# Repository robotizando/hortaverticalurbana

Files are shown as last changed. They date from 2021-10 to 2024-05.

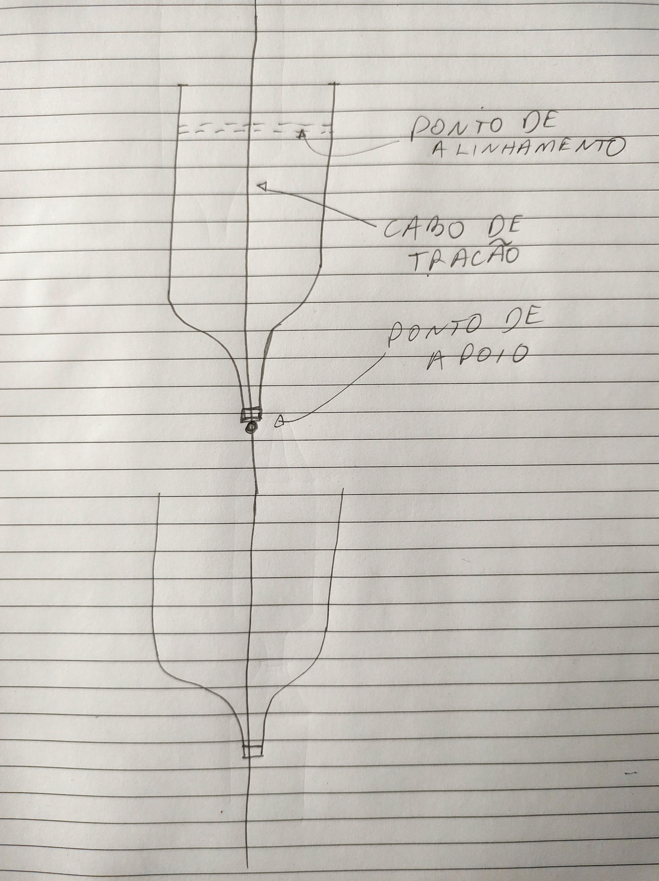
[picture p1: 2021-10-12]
Images/ponto de apoio invertido.jpg

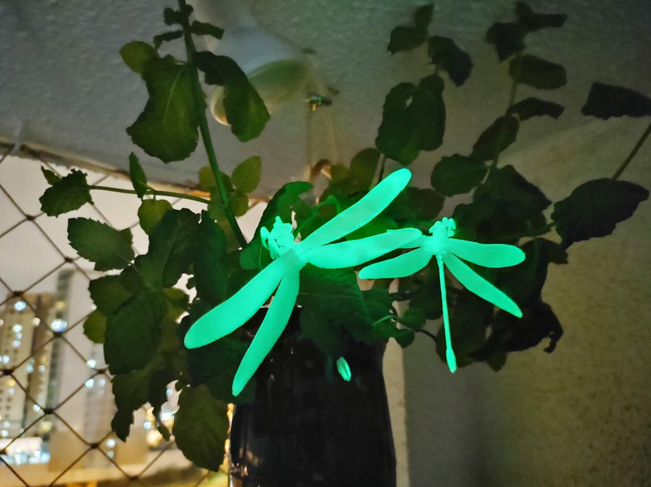
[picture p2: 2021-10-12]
Images/IMG_20210207_215612888_resized.jpg

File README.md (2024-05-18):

# Horta Vertical Urbana Livre

Repositório do material desenvolvido para a Horta Vertical Urbana

Veja o artigo completo **[no nosso site Robotizando](https://robotizando.com.br/pt-br/horta-vertical-urbana-livre/)**.

## Roadmap
- Terminar o sistema de agendamento de acionamento das cargas através de uma proto-linguagem

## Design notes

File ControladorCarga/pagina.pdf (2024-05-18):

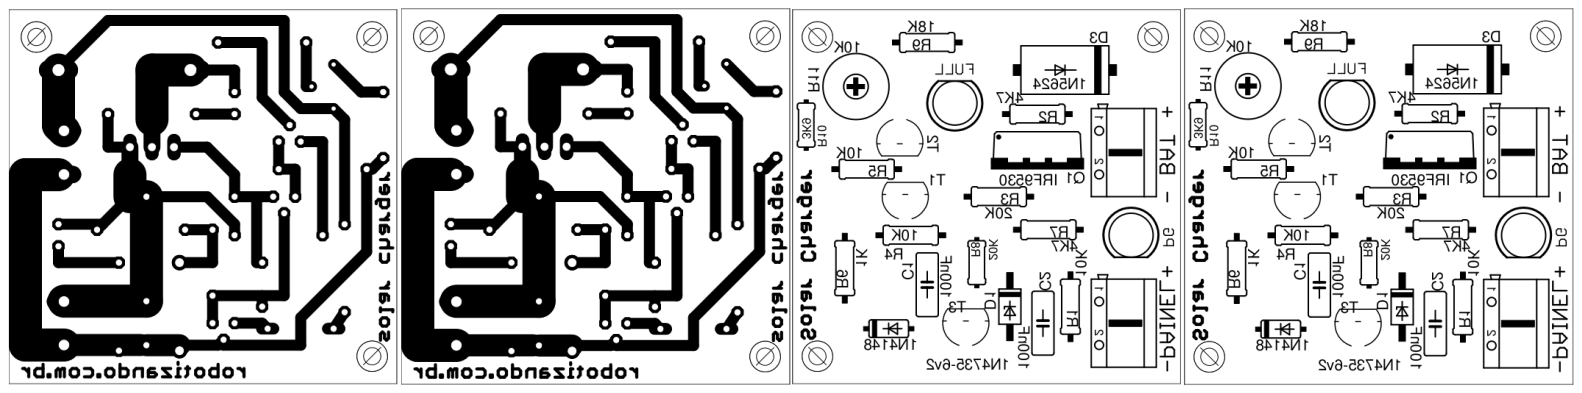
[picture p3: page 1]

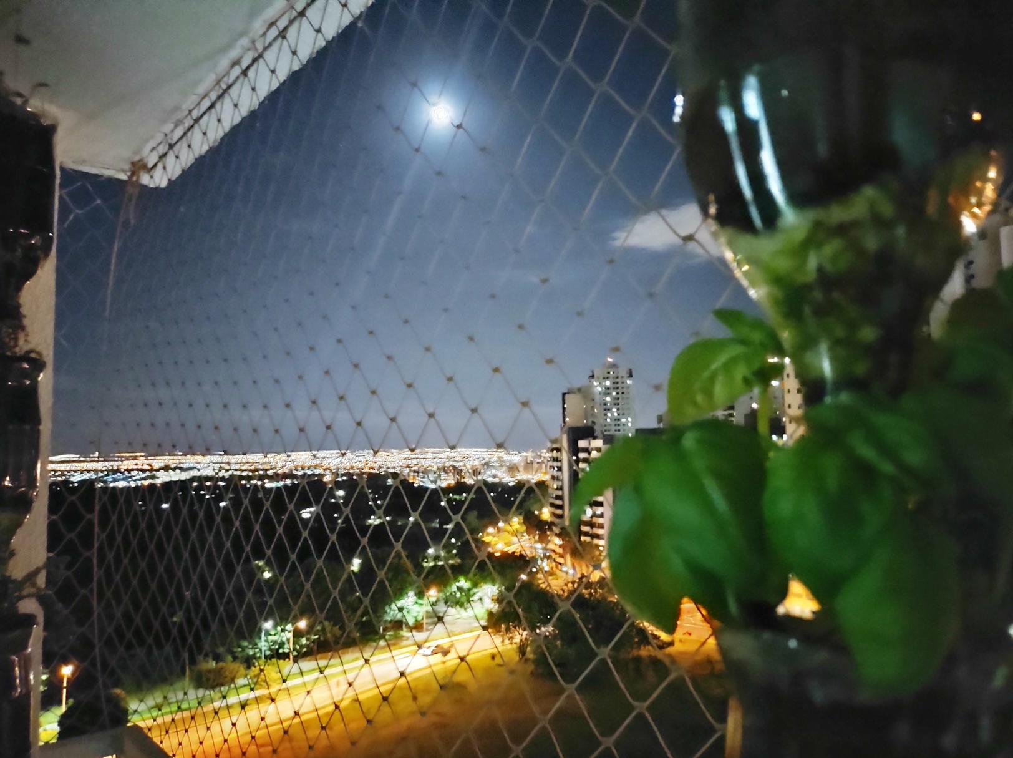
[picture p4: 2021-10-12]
Images/IMG_20210131_230912655_resized.jpg

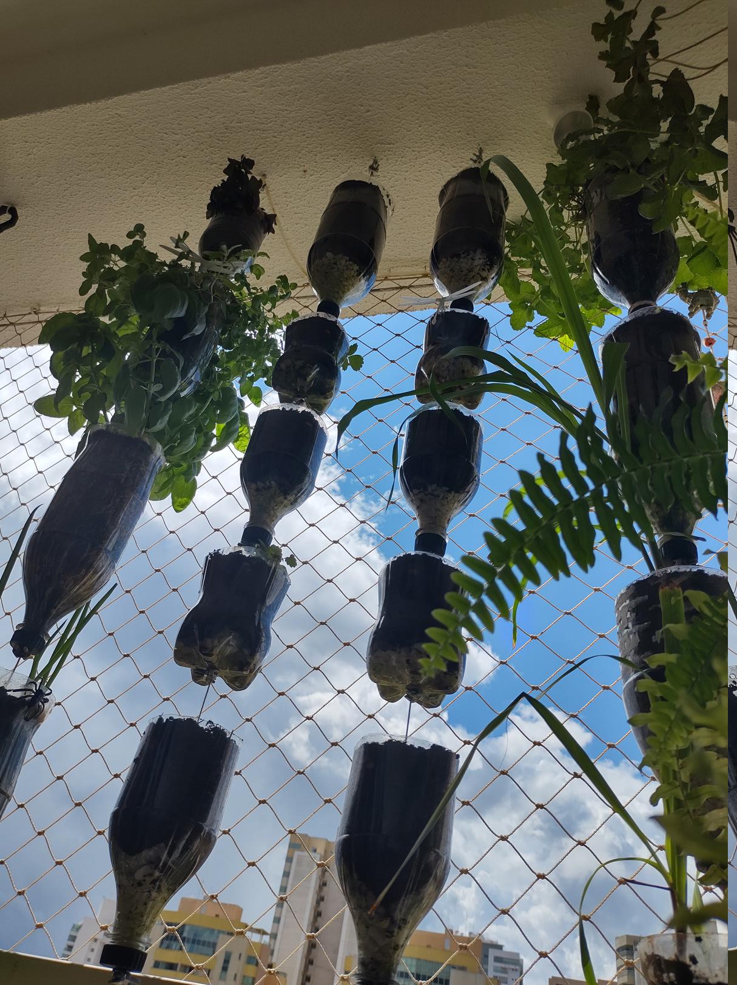
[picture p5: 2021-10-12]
Images/IMG_20210225_103853326_HDR_resized.jpg

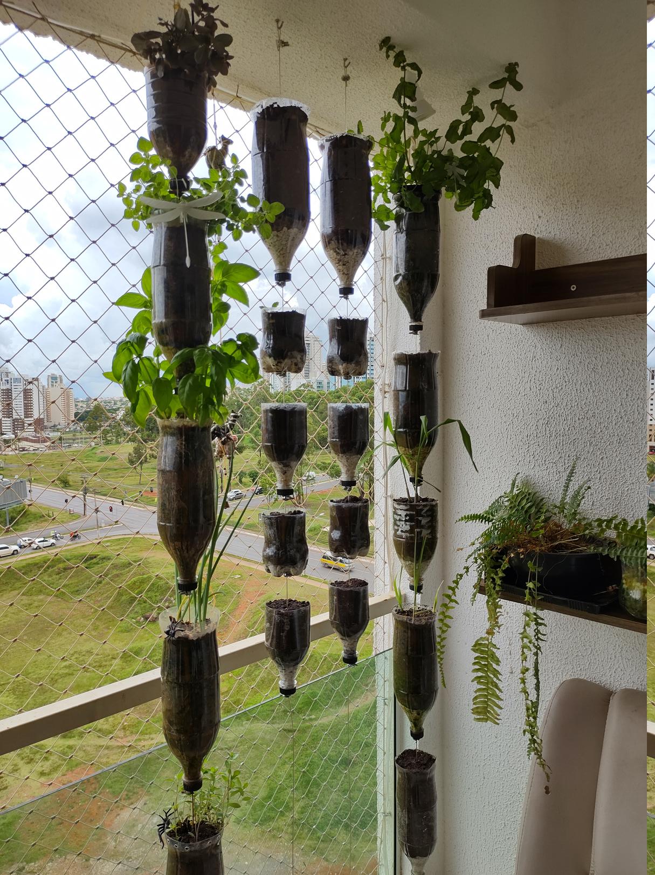
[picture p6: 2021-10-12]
Images/IMG_20210211_142128092_HDR_resized.jpg

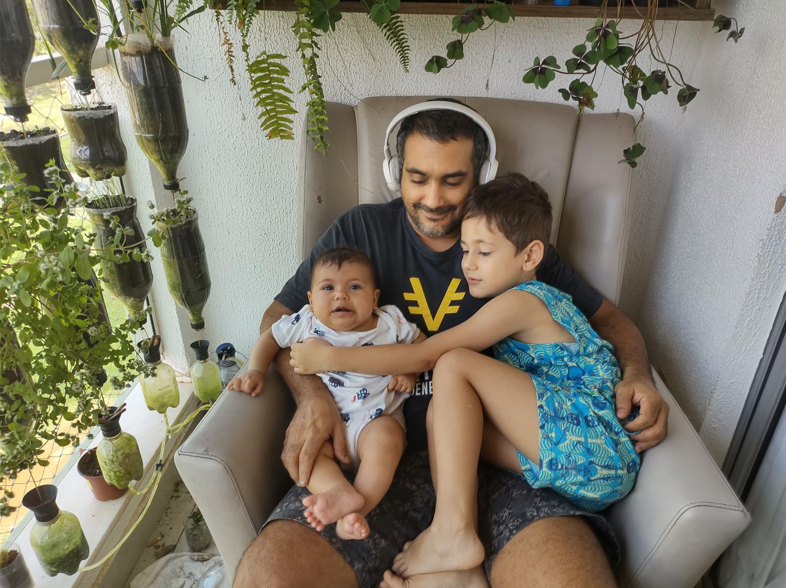
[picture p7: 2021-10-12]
Images/IMG_20210401_124431458_HDR_resized.jpg

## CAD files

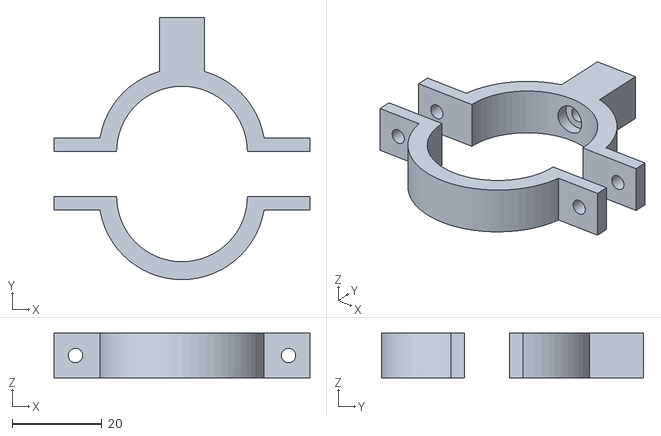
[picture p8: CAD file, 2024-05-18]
Pecas3D/caixa_holder.stl
57.2 x 58.6 x 10.0

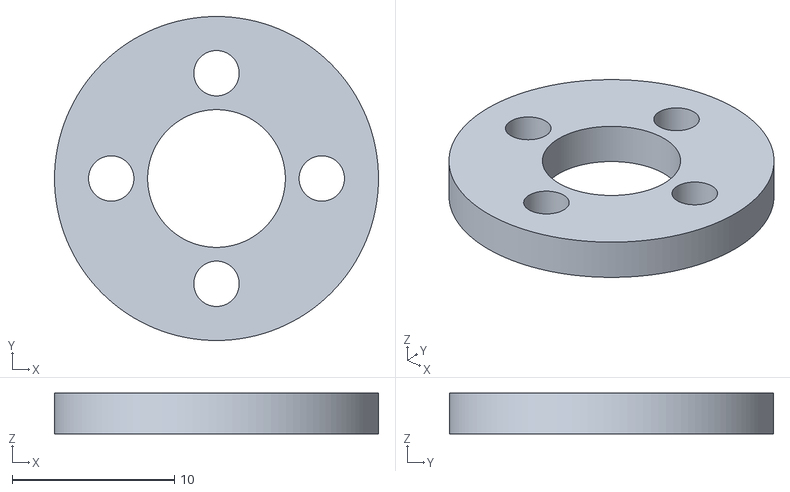
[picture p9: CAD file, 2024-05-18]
Pecas3D/respiro_pet_anel.stl
20.0 x 20.0 x 2.50

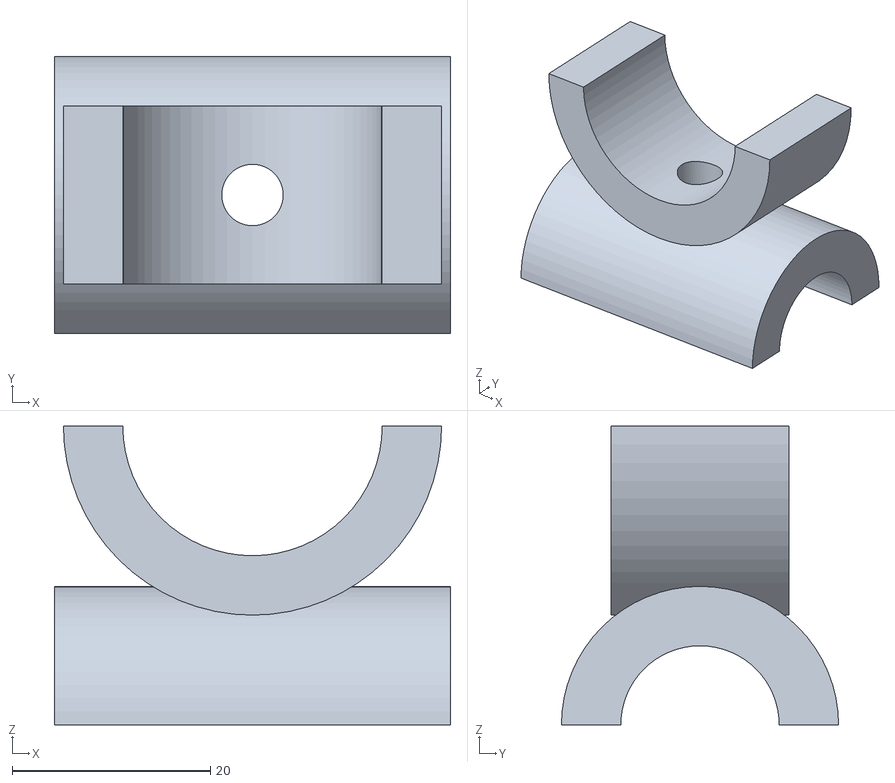
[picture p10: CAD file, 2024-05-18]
Pecas3D/trava_barra.stl
40.0 x 28.0 x 30.2

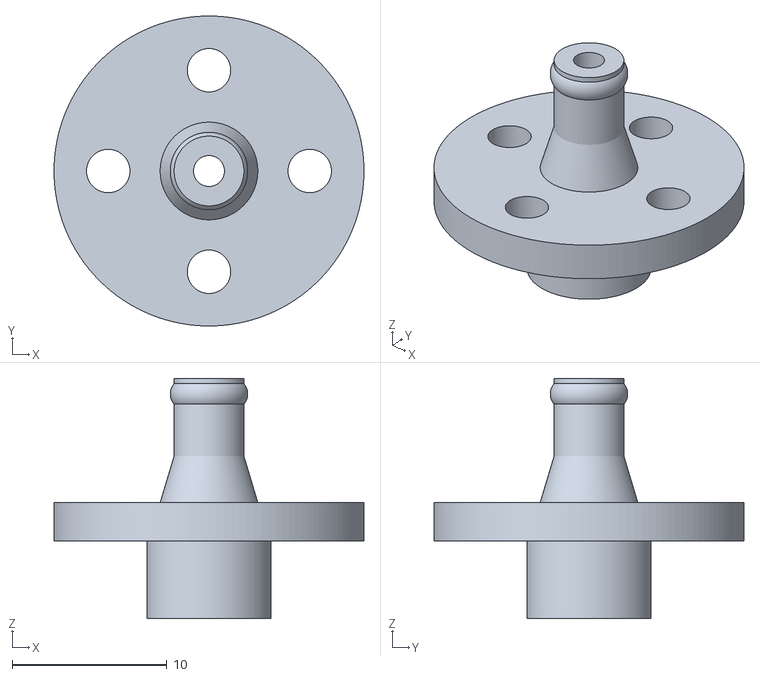
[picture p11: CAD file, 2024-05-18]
Pecas3D/respiro_pet_peca.stl
20.0 x 20.0 x 15.5

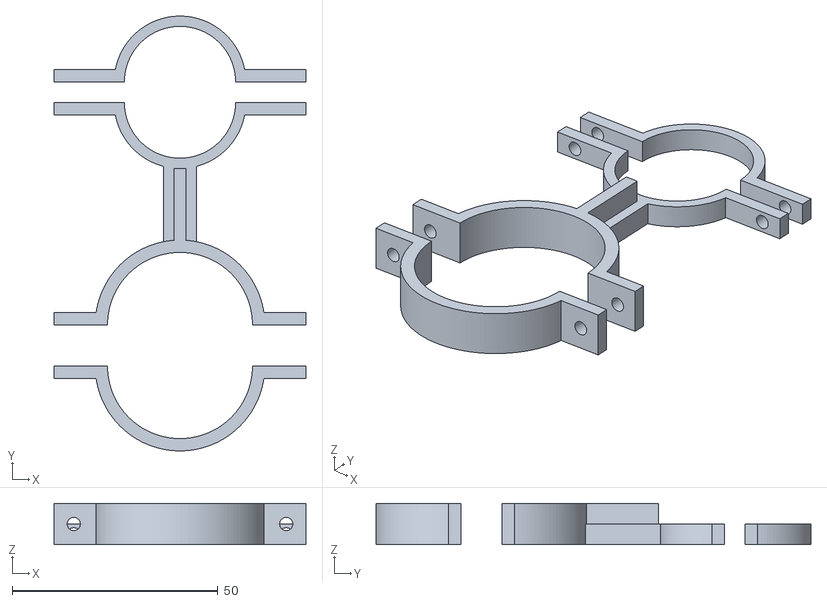
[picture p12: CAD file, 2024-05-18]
Pecas3D/buffer_superior_holder.stl
61.2 x 105.6 x 10.0

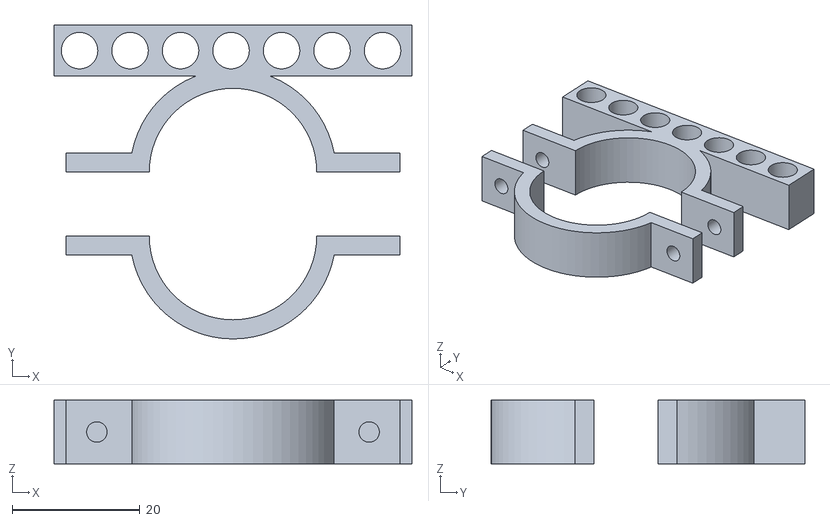
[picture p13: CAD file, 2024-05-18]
Pecas3D/canos_holder.stl
56.0 x 49.1 x 10.0

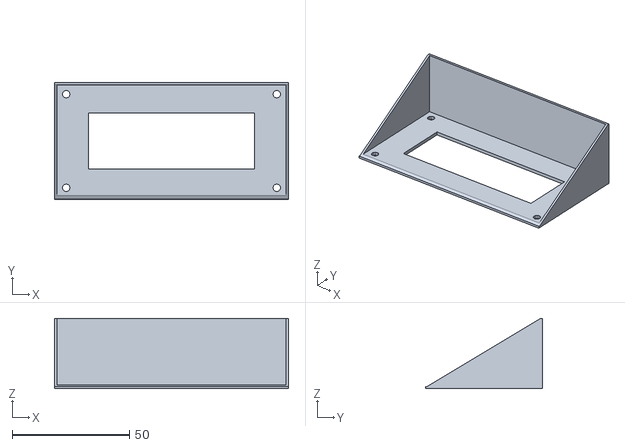
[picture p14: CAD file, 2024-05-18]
Pecas3D/ldc16x2sunshade.stl
100.0 x 50.0 x 30.0

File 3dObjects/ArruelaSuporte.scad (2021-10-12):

$fn=128;

hBase = 5;
dExterno = 45;
dInterno = 28.5;

dFuro = 6.5;


difference(){
    
    
    cylinder(h=hBase, r=dExterno/2);
    cylinder(h=hBase, r=dInterno/2);
    
    translate([-dInterno/2 - (dExterno-dInterno)/4 ,0,0])
    scale([0.6,1,1])
    cylinder(h=hBase, r=dFuro/2);

    translate([dInterno/2 + (dExterno-dInterno)/4 ,0,0])
    scale([0.6,1,1])
    cylinder(h=hBase, r=dFuro/2);

    translate([0 ,-dInterno/2 - (dExterno-dInterno)/4,0])
        scale([1,0.6,1])
    cylinder(h=hBase, r=dFuro/2);
    
    translate([0, dInterno/2 + (dExterno-dInterno)/4,0])
    scale([1,0.6,1])
    cylinder(h=hBase, r=dFuro/2);
    
}

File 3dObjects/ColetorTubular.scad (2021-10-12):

$fn=32;

dIntCone = 34;
dExtCone = dIntCone + 3;
hCone = 43;


hBico=8;
dIntBico=2.5;
dExtBico=5.1;

dIntAba = dExtCone;
dExtAba = dIntAba + 8;
hAba = 1;



*translate([0,0,hCone-0.1])
    tampa(bicos=1);




difference(){
    cylinder(h=hAba, r=dExtAba/2);
    cylinder(h=hAba, r=dIntAba/2);
}

difference(){
    cylinder(h=hCone, r=dExtCone/2);
    cylinder(h=hCone, r=dIntCone/2);

translate([dExtCone/2-3,25,3])
rotate([90,0,0])
cylinder(h=50,r=1);

translate([-dExtCone/2+3,25,3])
rotate([90,0,0])
cylinder(h=50,r=1);

}







module tampa(bicos=1){
  
    if(bicos==1){
        translate([0,0,dExtCone/2-1.7]){
            bico();
        }
    }
    
    if(bicos==2){
        translate([0,0,0]){
            translate([-5,0,dExtCone/2-3])
            bico();

            translate([5,0,dExtCone/2-3])
            bico();
        }
    }   
        
    difference(){

        sphere(r=dExtCone/2);
        sphere(r=dIntCone/2);
        
        if(bicos==2){
            translate([0,0,0]){
                translate([-5,0,dExtCone/2-5])
                bico(false);

                translate([5,0,dExtCone/2-5])
                bico(false);
            }
        }   
         
        if(bicos==1){
            translate([0,0,0]){
                translate([0,0,dExtCone/2-5])
                bico(false);
            }
        }
        
        translate([-dExtCone/2, -dExtCone/2,-dExtCone/2])
            cube([dExtCone,dExtCone,dExtCone/2]);    
    }
}




module bico(furado=true){
    difference(){
        
        render(){
            cylinder(h=hBico, r=dExtBico/2);
        
            translate([0,0, hBico-2])
            rotate_extrude(convexity = 10)
            translate([1.7, 0, 0])
            circle(r = 1, $fn = 100);
        }
        
        if(furado)
            cylinder(h=hBico, r=dIntBico/2);
    }
}

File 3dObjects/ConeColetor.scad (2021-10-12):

use <threadlib/threadlib.scad>



$fn = 256;

dBaseAro = 25;
dTopoAro = 45;
hCone = 25;
parede = 1.4;




*nut("PCO-1881", turns=3, Douter=34);



*difference(){
    import("3dponics-drip-nozzle-v2.stl");
    
    difference(){
        cylinder(h=10, r=30);
        cylinder(h=10, r=16.5);
    }    

    translate([0,0,9.95])
    color("red")
        cylinder(h=15.2, r=9);
}


//cone


translate([0,0,10]){

    //cone
    difference(){
        cylinder(h=hCone, r1=dBaseAro/2, r2=dTopoAro/2);
        cylinder(h=hCone, r1=(dBaseAro/2)-parede/2, r2=(dTopoAro/2)-parede/2);
    }


    //base
    dBase = 30;
    hBase = 1;
    dFuro = 2.5;
    difference(){
        cylinder(h=hBase, r=dBase/2);
        cylinder(h=hBase, r=dFuro/2);
        
        for ( i = [0 : 5] ){
            rotate( i * 60, [0, 0, 1])
            translate([-6.5,0,0])
            cylinder(h=hBase, r=dFuro/2);
        }
    }

    hPino = 5;
    dPino = 8;
    
    difference(){
        cylinder(h=hPino, r=dPino/2);
        cylinder(h=hPino, r=dFuro/2);
    }

    
    
}

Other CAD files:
3dObjects/ladrao01.scad
3dObjects/PontaGarrafa.scad
Pecas3D/buffer_superior_holder.scad
Pecas3D/caixa_holder.scad
Pecas3D/canos_holder.scad
Pecas3D/ldc16x2sunshade.scad
Pecas3D/respiro_pet.scad
Pecas3D/trava_barra.scad

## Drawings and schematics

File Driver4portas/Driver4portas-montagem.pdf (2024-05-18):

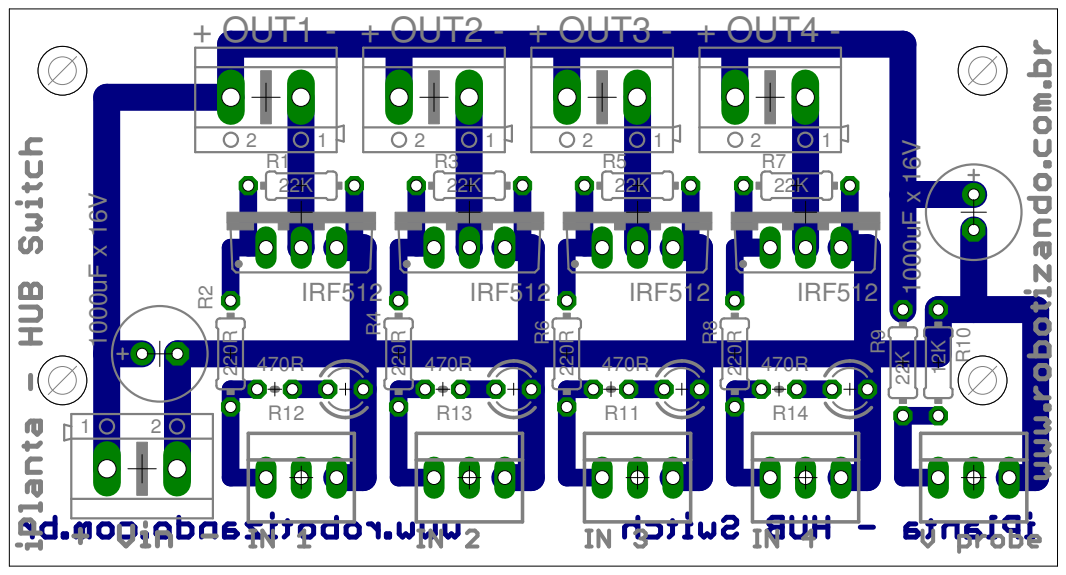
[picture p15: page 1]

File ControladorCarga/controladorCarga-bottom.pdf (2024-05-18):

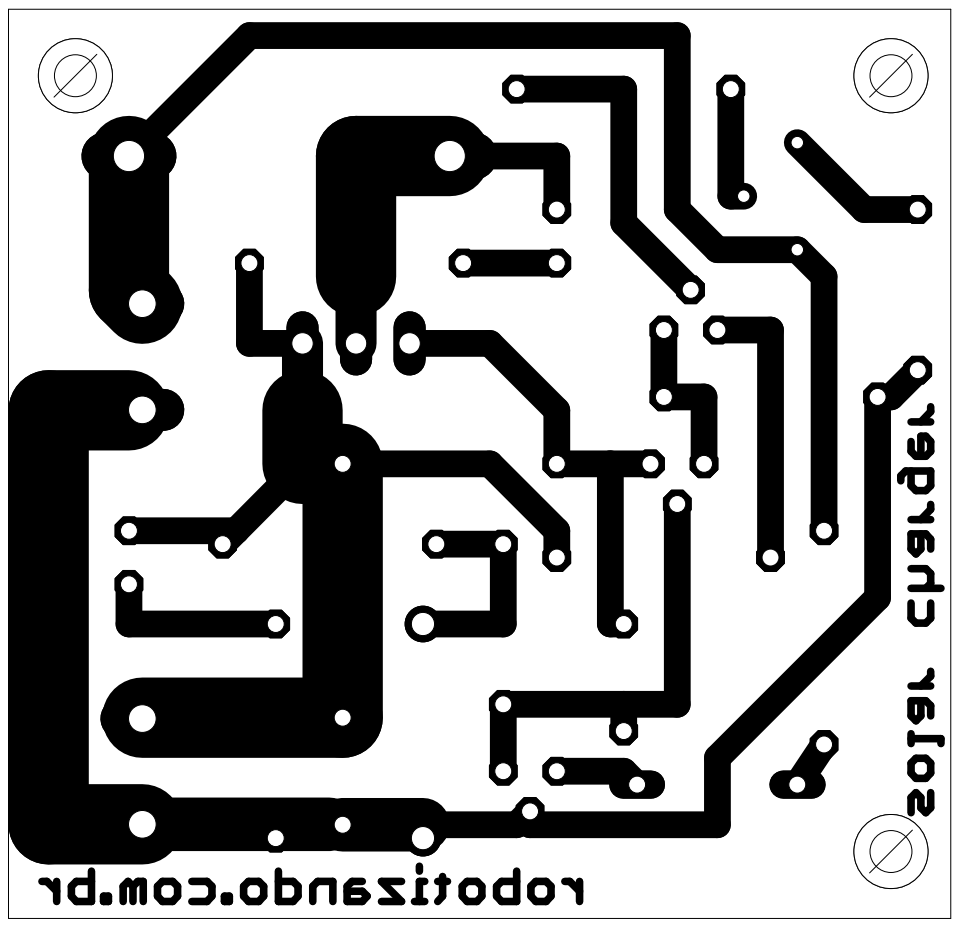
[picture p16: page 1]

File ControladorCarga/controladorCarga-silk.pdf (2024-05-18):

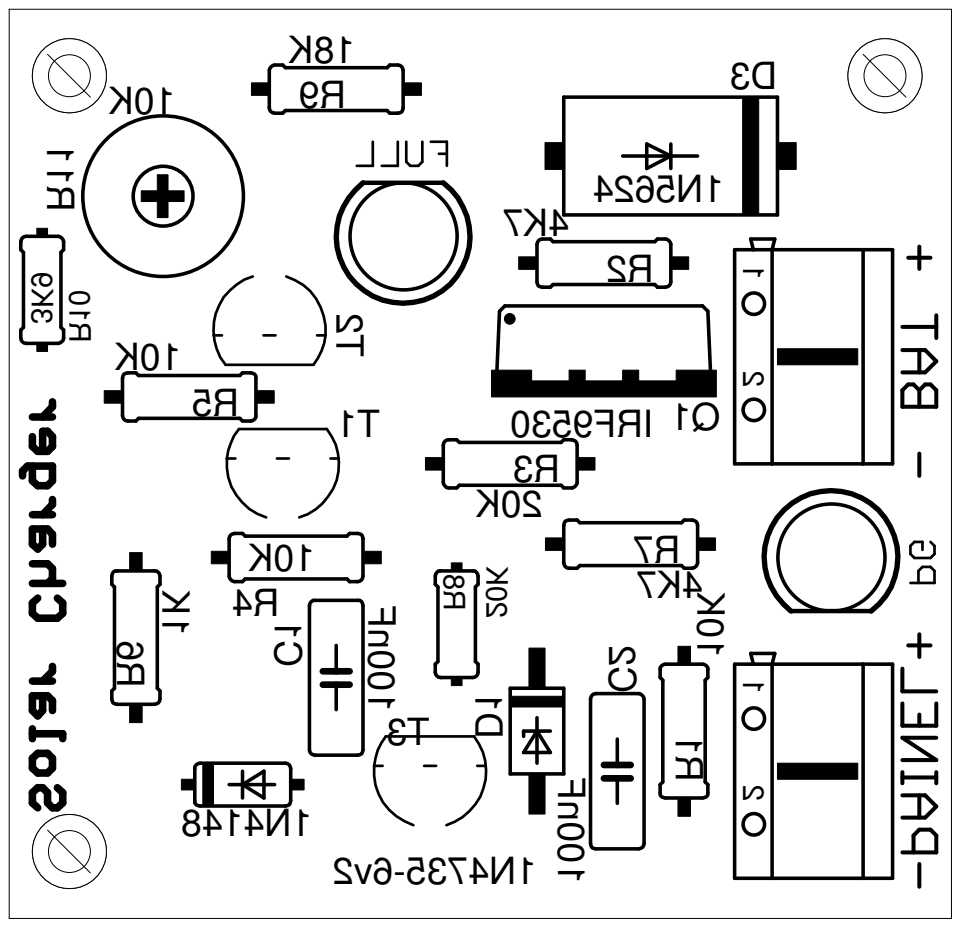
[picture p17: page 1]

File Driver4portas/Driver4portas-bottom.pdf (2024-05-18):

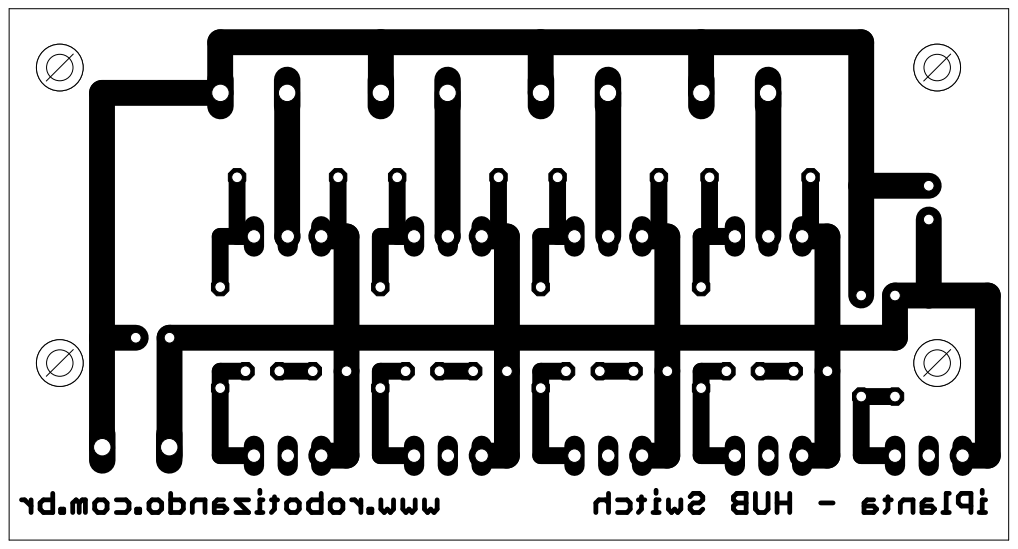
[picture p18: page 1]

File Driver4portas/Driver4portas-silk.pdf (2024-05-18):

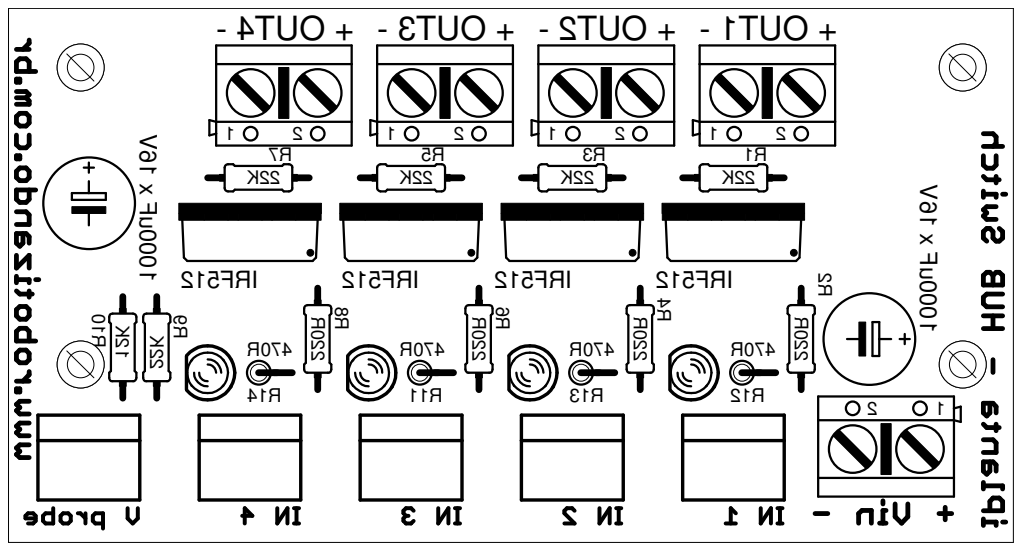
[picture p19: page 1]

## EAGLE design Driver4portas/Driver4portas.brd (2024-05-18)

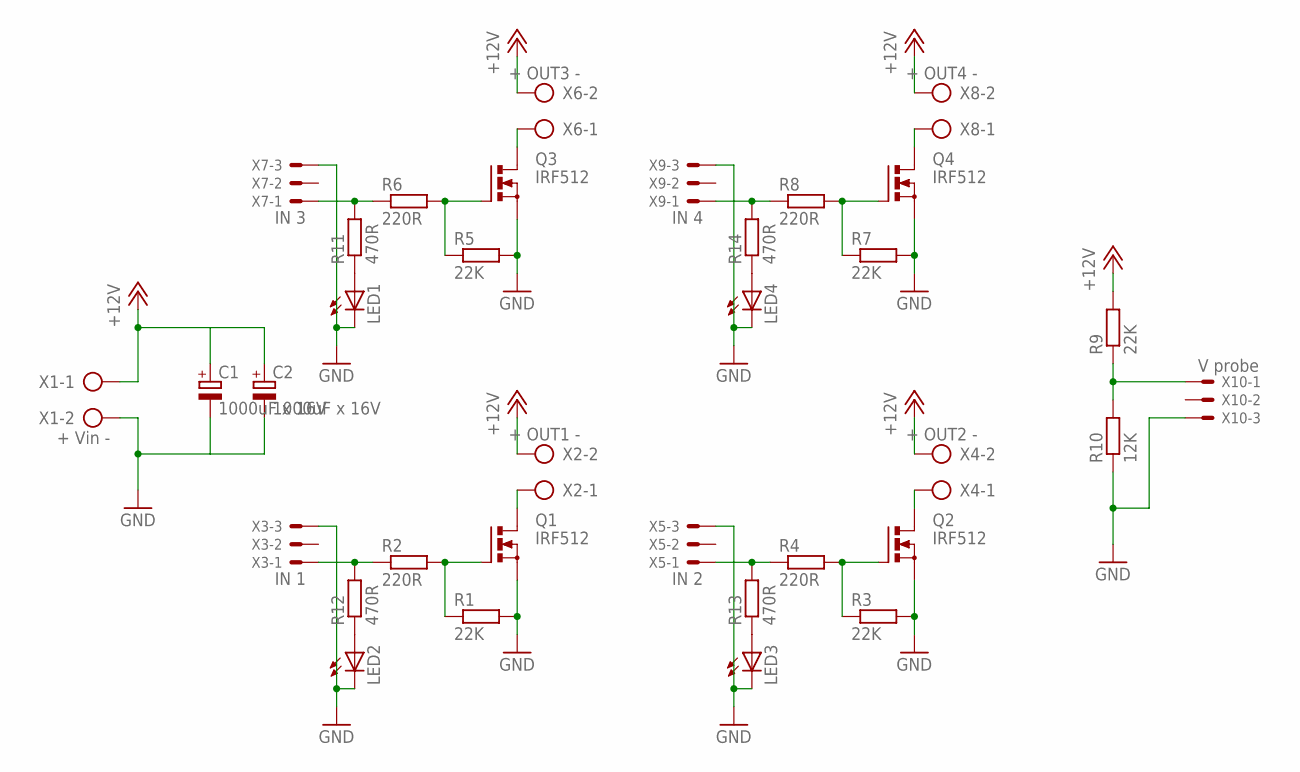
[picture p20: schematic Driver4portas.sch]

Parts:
C1, C2: 1000uF x 16V; E2,5-7
LED1, LED2, LED3, LED4: LED3MM
Q1, Q2, Q3, Q4: IRF512; TO220BV
R1, R3, R5, R7, R9: 22K; 0204/7
R2, R4, R6, R8: 220R; 0204/7
R10: 12K; 0204/7
R11, R12, R13, R14: 470R; 0204V
X1: + Vin -; AK500/2
X2: + OUT1 -; AK500/2
X3: IN 1; 22-23-2031
X4: + OUT2 -; AK500/2
X5: IN 2; 22-23-2031
X6: + OUT3 -; AK500/2
X7: IN 3; 22-23-2031
X8: + OUT4 -; AK500/2
X9: IN 4; 22-23-2031
X10: V probe; 22-23-2031

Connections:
+12V: C1.+, C2.+, R9.2, X1.1, X2.2, X4.2, X6.2, X8.2
GND: C1.-, C2.-, LED1.K (C), LED2.K (C), LED3.K (C), LED4.K (C), Q1.S, Q2.S, Q3.S, Q4.S, R1.2, R3.2, R5.2, R7.2, R10.1, X1.2, X3.3, X5.3, X7.3, X9.3, X10.3
unnamed: R2.1, R12.2, X3.1
unnamed: Q1.G, R1.1, R2.2
unnamed: Q1.D, X2.1
unnamed: Q2.G, R3.1, R4.2
unnamed: Q2.D, X4.1
unnamed: R4.1, R13.2, X5.1
unnamed: Q3.G, R5.1, R6.2
unnamed: Q3.D, X6.1
unnamed: R6.1, R11.2, X7.1
unnamed: Q4.G, R7.1, R8.2
unnamed: Q4.D, X8.1
unnamed: R8.1, R14.2, X9.1
unnamed: R9.1, R10.2, X10.1
unnamed: LED1.A, R11.1
unnamed: LED2.A, R12.1
unnamed: LED3.A, R13.1
unnamed: LED4.A, R14.1

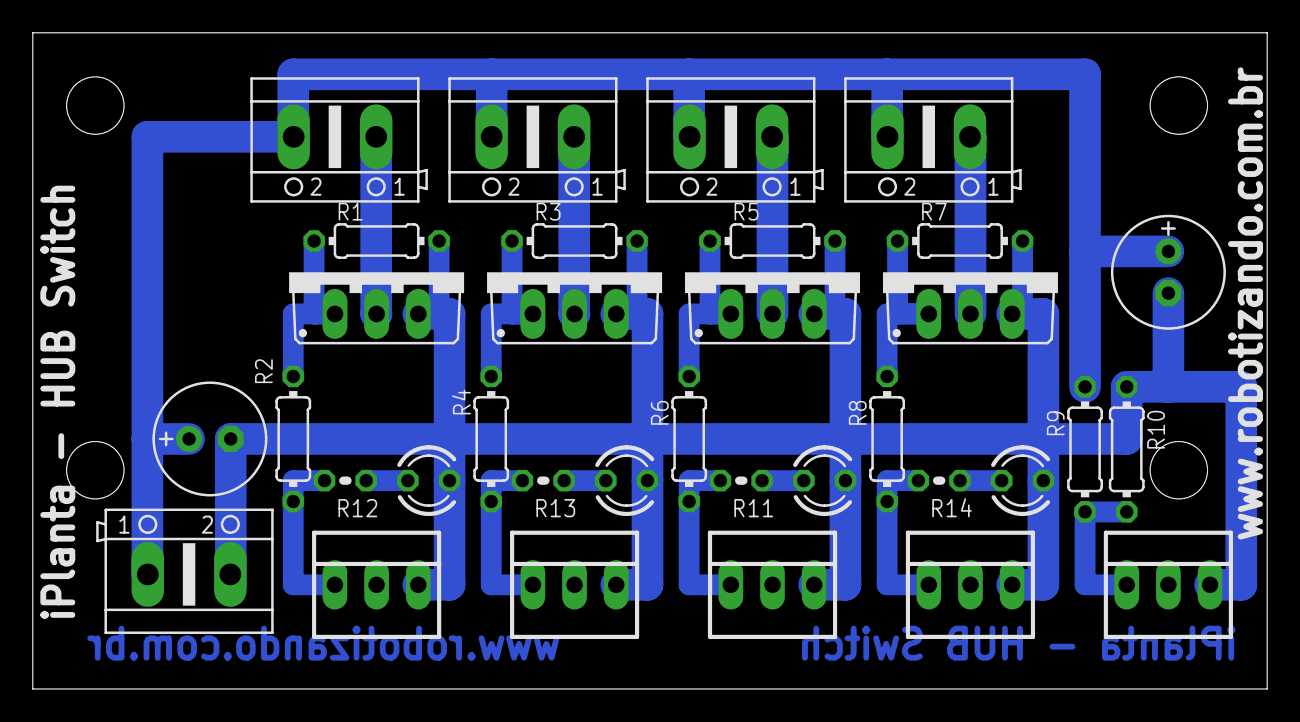
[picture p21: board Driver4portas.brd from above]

Board: 2 copper layers, 75.2 x 40.0 mm, 34 parts (0 on the bottom side), 19 nets.

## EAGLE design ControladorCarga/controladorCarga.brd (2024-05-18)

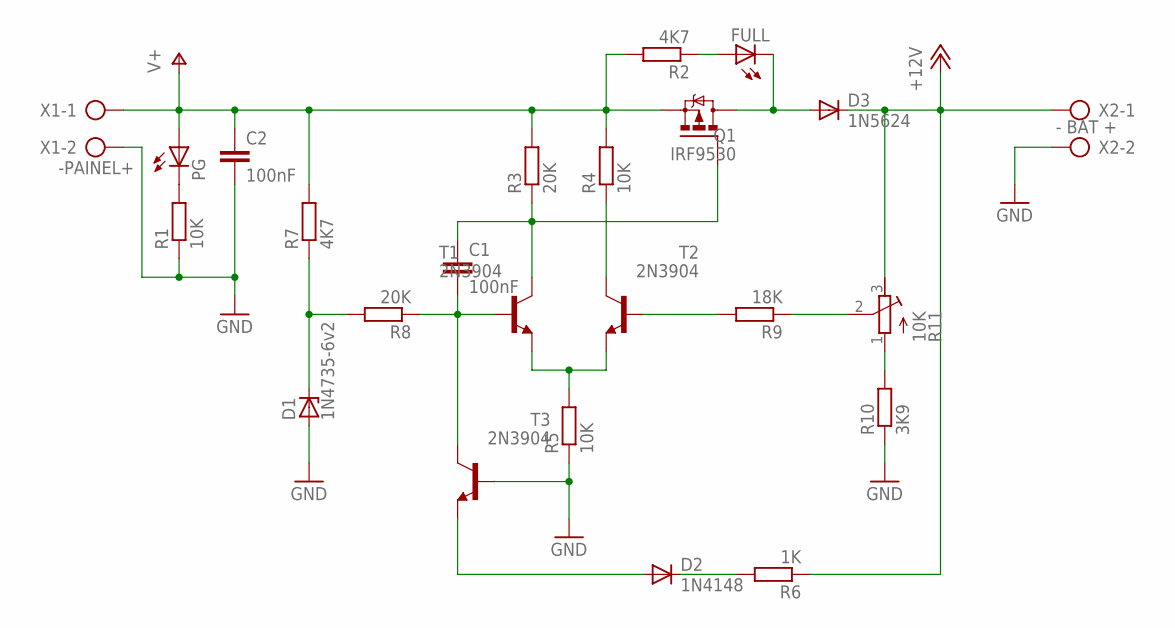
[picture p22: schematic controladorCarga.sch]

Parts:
C1, C2: 100nF; C050-025X075
D1: 1N4735-6v2; DO41Z10
D2: 1N4148; DO35-7
D3: 1N5624; DO201-15
FULL: LED5MM
PG: LED5MM
Q1: IRF9530; TO220BV
R1, R4, R5: 10K; 0207/10
R2, R7: 4K7; 0207/10
R3: 20K; 0207/10
R6: 1K; 0207/10
R8: 20K; 0204/7
R9: 18K; 0207/10
R10: 3K9; 0204/7
R11: 10K; RTRIM3339P
T1, T2, T3: 2N3904; TO92
X1: -PAINEL+; AK500/2
X2: - BAT +; AK500/2

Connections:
+12V: D3.C, R6.1, R11.3 (E), X2.1
GND: C2.2, D1.A, R1.1, R5.1, R10.1, T3.2 (B), X1.2, X2.2
unnamed: PG.K (C), R1.2
unnamed: FULL.A, R2.1
unnamed: C1.1, Q1.G, R3.1, T1.1 (C)
unnamed: R4.1, T2.1 (C)
unnamed: D2.C, R6.2
unnamed: R5.2, T1.3 (E), T2.3 (E)
unnamed: D3.A, FULL.K (C), Q1.D
unnamed: D1.C, R7.1, R8.2
unnamed: C1.2, R8.1, T1.2 (B), T3.1 (C)
unnamed: D2.A, T3.3 (E)
unnamed: R9.2, T2.2 (B)
unnamed: R9.1, R11.2 (S)
unnamed: R10.2, R11.1 (A)
V+: C2.1, PG.A, Q1.S, R2.2, R3.2, R4.2, R7.2, X1.1

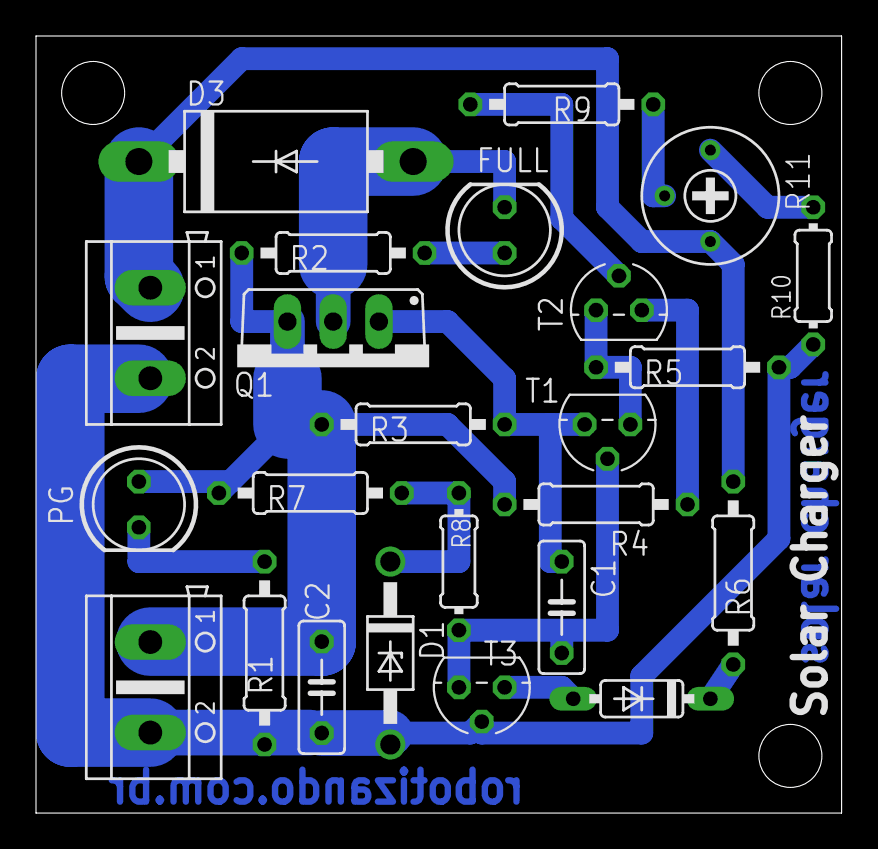
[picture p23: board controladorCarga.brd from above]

Board: 2 copper layers, 44.8 x 43.2 mm, 24 parts (0 on the bottom side), 16 nets.

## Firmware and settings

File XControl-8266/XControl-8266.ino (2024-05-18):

/*
  FSBrowser - A web-based FileSystem Browser for ESP8266 filesystems

  Copyright (c) 2015 Hristo Gochkov. All rights reserved.
  This file is part of the ESP8266WebServer library for Arduino environment.

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
  See readme.md for more information.
*/

////////////////////////////////
// Select the FileSystem by uncommenting one of the lines below

#define USE_SPIFFS
//#define USE_LITTLEFS
//#define USE_SDFS

#include <Arduino.h>
#include <ESP8266WiFi.h>
#include <ESP8266WiFiMulti.h>
#include <ESP8266WebServer.h>
#include <SPI.h>
#include <Wire.h>
#include <Adafruit_Sensor.h>
#include <Adafruit_BME280.h>
#include <ArduinoJson.h>
#include <NTPClient.h>
#include <WiFiUdp.h>
#include <Ticker.h>
#include <ESP8266HTTPClient.h>
#include <WiFiClientSecureBearSSL.h>


struct Config {
  char deviceUUID[64];
  int intervalPulse1;
  int schedulePulse1;
  int intervalPulse2;
  int schedulePulse2;
  int logCloudInterval;
};

const uint8_t fingerprint[20] = {0x94,0x57,0xC8,0xFE,0x33,0xB5,0x54,0xCE,0x29,0x84,0x14,0xDD,0x32,0xC1,0x48,0xF1,0x51,0x21,0xC5,0x51};


// ---------------
// NTP
// ---------------

const long utcOffsetInSeconds = -3 * 3600; //America_São Paulo

char daysOfTheWeek[7][12] = {"Sunday", "Monday", "Tuesday", "Wednesday", "Thursday", "Friday", "Saturday"};

// Define NTP Client to get time
WiFiUDP ntpUDP;
NTPClient timeClient(ntpUDP, "pool.ntp.org", utcOffsetInSeconds);

unsigned long currentTime;


// ---------------
// Timers
// ---------------

#define DATALOG_UPDATE_INTERVAL 60
Ticker dataLogTimer;

#define CHECK_ALARM_INTERVAL 1
Ticker checkAlarmTimer;


// ---------------
// GENERAL IO
// ---------------

#define IRRIGA 0
#define ILUMINA 1

int relesPins[] = {D0,D3};
#define relesQtd  2

const int batteryPin = A0;
int batteryValue = 0;  // value read from the pot

void output(int index, int value){
    digitalWrite(relesPins[index], !value);
}

double voltsPerUnit = 0.04;
int adoffset = 8;


int irrigaStatus = LOW;
int iluminaStatus = LOW;

// ---------------
// BME280
// ---------------

#define SEALEVELPRESSURE_HPA (1013.25)

Adafruit_BME280 bme;

float temperature, humidity, pressure, altitude;

void updateBME(){
  temperature = bme.readTemperature();
  humidity = bme.readHumidity();
  pressure = bme.readPressure() / 100.0F;
  altitude = bme.readAltitude(SEALEVELPRESSURE_HPA);
}

// ---------------
// FILE SYSTEM
// ---------------

#if defined USE_SPIFFS
  #include <FS.h>
  const char* fsName = "SPIFFS";
  FS* fileSystem = &SPIFFS;
  SPIFFSConfig fileSystemConfig = SPIFFSConfig();
#elif defined USE_LITTLEFS
  #include <LittleFS.h>
  const char* fsName = "LittleFS";
  FS* fileSystem = &LittleFS;
  LittleFSConfig fileSystemConfig = LittleFSConfig();
#elif defined USE_SDFS
  #include <SDFS.h>
  const char* fsName = "SDFS";
  FS* fileSystem = &SDFS;
  SDFSConfig fileSystemConfig = SDFSConfig();
  //fileSystemConfig.setCSPin(chipSelectPin);
#else
#error Please select a filesystem first by uncommenting one of the "#define USE_xxx" lines at the beginning of the sketch.
#endif


#define DBG_OUTPUT_PORT Serial



// ---------------
// SYSTEM CONFIGURATION FILE
// ---------------

const char *configFile = "/config.json";
Config config;

// Loads the configuration from a file
void loadConfiguration(const char *filename, Config &config) {

  Serial.println(F("Loading configuration File"));

  File file = fileSystem->open(filename, "r");

  // Allocate a temporary JsonDocument
  // Don't forget to change the capacity to match your requirements.
  // Use arduinojson.org/v6/assistant to compute the capacity.
  StaticJsonDocument<512> doc;

  // Deserialize the JSON document
  DeserializationError error = deserializeJson(doc, file);
  if (error){
    Serial.println(F("Failed to read file, using default configuration"));
    strlcpy(config.deviceUUID,"", sizeof(config.deviceUUID));
    config.intervalPulse1 = 0;
    config.schedulePulse1 = 0;
    config.intervalPulse2 = 0;
    config.schedulePulse2 = 0;
    config.logCloudInterval = 0;
  } else {
    // Copy values from the JsonDocument to the Config
    strlcpy(config.deviceUUID, doc["deviceUUID"], sizeof(config.deviceUUID));
    config.intervalPulse1 = doc["intervalPulse1"];
    config.schedulePulse1 = doc["schedulePulse1"];
    config.intervalPulse2 = doc["intervalPulse2"];
    config.schedulePulse2 = doc["schedulePulse2"];
    config.logCloudInterval = doc["logCloudInterval"];
  }

  file.close();
  Serial.println(F("Configuration file loaded"));
}



#ifndef STASSID
#define STASSID "FamiliaTeo"
#define STAPSK  "aguadoce"
#endif

const char* ssid = STASSID;
const char* password = STAPSK;
const char* host = "XControl";

ESP8266WebServer server(80);

static bool fsOK;
String unsupportedFiles = String();

File uploadFile;

static const char TEXT_PLAIN[] PROGMEM = "text/plain";
static const char FS_INIT_ERROR[] PROGMEM = "FS INIT ERROR";
static const char FILE_NOT_FOUND[] PROGMEM = "FileNotFound";

////////////////////////////////
// Utils to return HTTP codes, and determine content-type

void replyOK() {
  server.send(200, FPSTR(TEXT_PLAIN), "");
}

void replyOKWithMsg(String msg) {
  server.send(200, FPSTR(TEXT_PLAIN), msg);
}

void replyNotFound(String msg) {
  server.send(404, FPSTR(TEXT_PLAIN), msg);
}

void replyBadRequest(String msg) {
  DBG_OUTPUT_PORT.println(msg);
  server.send(400, FPSTR(TEXT_PLAIN), msg + "\r\n");
}

void replyServerError(String msg) {
  DBG_OUTPUT_PORT.println(msg);
  server.send(500, FPSTR(TEXT_PLAIN), msg + "\r\n");
}

#ifdef USE_SPIFFS
/*
   Checks filename for character combinations that are not supported by FSBrowser (alhtough valid on SPIFFS).
   Returns an empty String if supported, or detail of error(s) if unsupported
*/
String checkForUnsupportedPath(String filename) {
  String error = String();
  if (!filename.startsWith("/")) {
    error += F("!NO_LEADING_SLASH! ");
  }
  if (filename.indexOf("//") != -1) {
    error += F("!DOUBLE_SLASH! ");
  }
  if (filename.endsWith("/")) {
    error += F("!TRAILING_SLASH! ");
  }
  return error;
}
#endif


////////////////////////////////
// Request handlers

/*
   Return the FS type, status and size info
*/
void handleStatus() {
  DBG_OUTPUT_PORT.println("handleStatus");
  FSInfo fs_info;
  String json;
  json.reserve(128);

  json = "{\"type\":\"";
  json += fsName;
  json += "\", \"isOk\":";
  if (fsOK) {
    fileSystem->info(fs_info);
    json += F("\"true\", \"totalBytes\":\"");
    json += fs_info.totalBytes;
    json += F("\", \"usedBytes\":\"");
    json += fs_info.usedBytes;
    json += "\"";
  } else {
    json += "\"false\"";
  }
  json += F(",\"unsupportedFiles\":\"");
  json += unsupportedFiles;
  json += "\"}";

  server.send(200, "application/json", json);
}


/*
   Return the list of files in the directory specified by the "dir" query string parameter.
   Also demonstrates the use of chuncked responses.
*/
void handleFileList() {
  if (!fsOK) {
    return replyServerError(FPSTR(FS_INIT_ERROR));
  }

  if (!server.hasArg("dir")) {
    return replyBadRequest(F("DIR ARG MISSING"));
  }

  String path = server.arg("dir");
  if (path != "/" && !fileSystem->exists(path)) {
    return replyBadRequest("BAD PATH");
  }

  DBG_OUTPUT_PORT.println(String("handleFileList: ") + path);
  Dir dir = fileSystem->openDir(path);
  path.clear();

  // use HTTP/1.1 Chunked response to avoid building a huge temporary string
  if (!server.chunkedResponseModeStart(200, "text/json")) {
    server.send(505, F("text/html"), F("HTTP1.1 required"));
    return;
  }

  // use the same string for every line
  String output;
  output.reserve(64);
  while (dir.next()) {
#ifdef USE_SPIFFS
    String error = checkForUnsupportedPath(dir.fileName());
    if (error.length() > 0) {
      DBG_OUTPUT_PORT.println(String("Ignoring ") + error + dir.fileName());
      continue;
    }
#endif
    if (output.length()) {
      // send string from previous iteration
      // as an HTTP chunk
      server.sendContent(output);
      output = ',';
    } else {
      output = '[';
    }

    output += "{\"type\":\"";
    if (dir.isDirectory()) {
      output += "dir";
    } else {
      output += F("file\",\"size\":\"");
      output += dir.fileSize();
    }

    output += F("\",\"name\":\"");
    // Always return names without leading "/"
    if (dir.fileName()[0] == '/') {
      output += &(dir.fileName()[1]);
    } else {
      output += dir.fileName();
    }

    output += "\"}";
  }

  // send last string
  output += "]";
  server.sendContent(output);
  server.chunkedResponseFinalize();
}


/*
   Read the given file from the filesystem and stream it back to the client
*/
bool handleFileRead(String path) {
  DBG_OUTPUT_PORT.println(String("handleFileRead: ") + path);
  if (!fsOK) {
    replyServerError(FPSTR(FS_INIT_ERROR));
    return true;
  }

  if (path.endsWith("/")) {
    path += "index.htm";
  }

  String contentType;
  if (server.hasArg("download")) {
    contentType = F("application/octet-stream");
  } else {
    contentType = mime::getContentType(path);
  }

  if (!fileSystem->exists(path)) {
    // File not found, try gzip version
    path = path + ".gz";
  }
  if (fileSystem->exists(path)) {
    File file = fileSystem->open(path, "r");
    if (server.streamFile(file, contentType) != file.size()) {
      DBG_OUTPUT_PORT.println("Sent less data than expected!");
    }
    file.close();
    return true;
  }

  return false;
}


/*
   As some FS (e.g. LittleFS) delete the parent folder when the last child has been removed,
   return the path of the closest parent still existing
*/
String lastExistingParent(String path) {
  while (!path.isEmpty() && !fileSystem->exists(path)) {
    if (path.lastIndexOf('/') > 0) {
      path = path.substring(0, path.lastIndexOf('/'));
    } else {
      path = String();  // No slash => the top folder does not exist
    }
  }
  DBG_OUTPUT_PORT.println(String("Last existing parent: ") + path);
  return path;
}

/*
   Handle the creation/rename of a new file
   Operation      | req.responseText
   ---------------+--------------------------------------------------------------
   Create file    | parent of created file
   Create folder  | parent of created folder
   Rename file    | parent of source file
   Move file      | parent of source file, or remaining ancestor
   Rename folder  | parent of source folder
   Move folder    | parent of source folder, or remaining ancestor
*/
void handleFileCreate() {
  if (!fsOK) {
    return replyServerError(FPSTR(FS_INIT_ERROR));
  }

  String path = server.arg("path");
  if (path.isEmpty()) {
    return replyBadRequest(F("PATH ARG MISSING"));
  }

#ifdef USE_SPIFFS
  if (checkForUnsupportedPath(path).length() > 0) {
    return replyServerError(F("INVALID FILENAME"));
  }
#endif

  if (path == "/") {
    return replyBadRequest("BAD PATH");
  }
  if (fileSystem->exists(path)) {
    return replyBadRequest(F("PATH FILE EXISTS"));
  }

  String src = server.arg("src");
  if (src.isEmpty()) {
    // No source specified: creation
    DBG_OUTPUT_PORT.println(String("handleFileCreate: ") + path);
    if (path.endsWith("/")) {
      // Create a folder
      path.remove(path.length() - 1);
      if (!fileSystem->mkdir(path)) {
        return replyServerError(F("MKDIR FAILED"));
      }
    } else {
      // Create a file
      File file = fileSystem->open(path, "w");
      if (file) {
        file.write((const char *)0);
        file.close();
      } else {
        return replyServerError(F("CREATE FAILED"));
      }
    }
    if (path.lastIndexOf('/') > -1) {
      path = path.substring(0, path.lastIndexOf('/'));
    }
    replyOKWithMsg(path);
  } else {
    // Source specified: rename
    if (src == "/") {
      return replyBadRequest("BAD SRC");
    }
    if (!fileSystem->exists(src)) {
      return replyBadRequest(F("SRC FILE NOT FOUND"));
    }

    DBG_OUTPUT_PORT.println(String("handleFileCreate: ") + path + " from " + src);

    if (path.endsWith("/")) {
      path.remove(path.length() - 1);
    }
    if (src.endsWith("/")) {
      src.remove(src.length() - 1);
    }
    if (!fileSystem->rename(src, path)) {
      return replyServerError(F("RENAME FAILED"));
    }
    replyOKWithMsg(lastExistingParent(src));
  }
}


/*
   Delete the file or folder designed by the given path.
   If it's a file, delete it.
   If it's a folder, delete all nested contents first then the folder itself

   IMPORTANT NOTE: using recursion is generally not recommended on embedded devices and can lead to crashes (stack overflow errors).
   This use is just for demonstration purpose, and FSBrowser might crash in case of deeply nested filesystems.
   Please don't do this on a production system.
*/
void deleteRecursive(String path) {
  File file = fileSystem->open(path, "r");
  bool isDir = file.isDirectory();
  file.close();

  // If it's a plain file, delete it
  if (!isDir) {
    fileSystem->remove(path);
    return;
  }

  // Otherwise delete its contents first
  Dir dir = fileSystem->openDir(path);

  while (dir.next()) {
    deleteRecursive(path + '/' + dir.fileName());
  }

  // Then delete the folder itself
  fileSystem->rmdir(path);
}


/*
   Handle a file deletion request
   Operation      | req.responseText
   ---------------+--------------------------------------------------------------
   Delete file    | parent of deleted file, or remaining ancestor
   Delete folder  | parent of deleted folder, or remaining ancestor
*/


/*
   Handle a file upload request
*/
void handleFileUpload() {
  if (!fsOK) {
    return replyServerError(FPSTR(FS_INIT_ERROR));
  }
  if (server.uri() != "/edit") {
    return;
  }
  HTTPUpload& upload = server.upload();
  if (upload.status == UPLOAD_FILE_START) {
    String filename = upload.filename;
    // Make sure paths always start with "/"
    if (!filename.startsWith("/")) {
      filename = "/" + filename;
    }
    DBG_OUTPUT_PORT.println(String("handleFileUpload Name: ") + filename);
    uploadFile = fileSystem->open(filename, "w");
    if (!uploadFile) {
      return replyServerError(F("CREATE FAILED"));
    }
    DBG_OUTPUT_PORT.println(String("Upload: START, filename: ") + filename);
  } else if (upload.status == UPLOAD_FILE_WRITE) {
    if (uploadFile) {
      size_t bytesWritten = uploadFile.write(upload.buf, upload.currentSize);
      if (bytesWritten != upload.currentSize) {
        return replyServerError(F("WRITE FAILED"));
      }
    }
    DBG_OUTPUT_PORT.println(String("Upload: WRITE, Bytes: ") + upload.currentSize);
  } else if (upload.status == UPLOAD_FILE_END) {
    if (uploadFile) {
      uploadFile.close();
    }
    DBG_OUTPUT_PORT.println(String("Upload: END, Size: ") + upload.totalSize);
  }
}


void handleFile(String file) {
  if (!fsOK) {
    return replyServerError(FPSTR(FS_INIT_ERROR));
  }

  if (handleFileRead(file)) {
    return;
  }
    // Dump debug data
  String message;
  message.reserve(100);
  message = F("Error: File not found\n\nURI: ");
  message += file;
  message += F("\nMethod: ");
  message += (server.method() == HTTP_GET) ? "GET" : "POST";
  message += F("\nArguments: ");
  message += server.args();
  message += '\n';
  for (uint8_t i = 0; i < server.args(); i++) {
    message += F(" NAME:");
    message += server.argName(i);
    message += F("\n VALUE:");
    message += server.arg(i);
    message += '\n';
  }
  message += "path=";
  message += server.arg("path");
  message += '\n';
  DBG_OUTPUT_PORT.print(message);

  return replyNotFound(message);
  
}

/*
   The "Not Found" handler catches all URI not explicitely declared in code
   First try to find and return the requested file from the filesystem,
   and if it fails, return a 404 page with debug information
*/
void handleNotFound() {
  if (!fsOK) {
    return replyServerError(FPSTR(FS_INIT_ERROR));
  }

  String uri = ESP8266WebServer::urlDecode(server.uri()); // required to read paths with blanks

  handleFile(uri);
}

void handleIndex(){
  handleFile("/index.html");
}



/*
   This specific handler returns the index.htm (or a gzipped version) from the /edit folder.
   If the file is not present but the flag INCLUDE_FALLBACK_INDEX_HTM has been set, falls back to the version
   embedded in the program code.
   Otherwise, fails with a 404 page with debug information
*/
void handleGetEdit() {
  if (handleFileRead(F("/edit/index.htm"))) {
    return;
  }

#ifdef INCLUDE_FALLBACK_INDEX_HTM
  server.sendHeader(F("Content-Encoding"), "gzip");
  server.send(200, "text/html", index_htm_gz, index_htm_gz_len);
#else
  replyNotFound(FPSTR(FILE_NOT_FOUND));
#endif

}

ESP8266WiFiMulti wiFiMulti;
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
void loop(void) {
  server.handleClient();

  //It must be in the main loop :-P
  if( postToCloud ){
     
     updateBME();
     batteryValue = analogRead(batteryPin);

    std::unique_ptr<BearSSL::WiFiClientSecure>client(new BearSSL::WiFiClientSecure);
    client->setFingerprint(fingerprint);
    HTTPClient https;

    String path;
    path.reserve(256);
    path = "https://robotizando.com.br/xcontrol/log.php?did=";
    path += config.deviceUUID;
    path += "&t=";
    path += temperature;
    path += "&u=";
    path += humidity;
    path += "&p=";
    path += pressure;
    path += "&b=";
    path += (batteryValue-adoffset)*voltsPerUnit;

    if (https.begin(*client, path.c_str())) {  // HTTPS
        Serial.print("[HTTPS] GET...\n");
        // start connection and send HTTP header
        int httpCode = https.GET();
  
        // httpCode will be negative on error
        if (httpCode > 0) {
          // HTTP header has been send and Server response header has been handled
          Serial.printf("[HTTPS] GET... code: %d\n", httpCode);
  
          // file found at server
          if (httpCode == HTTP_CODE_OK || httpCode == HTTP_CODE_MOVED_PERMANENTLY) {
            String payload = https.getString();
            if( payload.equals("rega") ){
                output( IRRIGA, HIGH );
                irrigaStatus = HIGH;
                delay(config.intervalPulse1*1000);
                output( IRRIGA, LOW );
                irrigaStatus = LOW;
            }
            
            Serial.println(payload);
          }
        } else {
          Serial.printf("[HTTPS] GET... failed, error: %s\n", https.errorToString(httpCode).c_str());
        }
        https.end();
     } else {
        Serial.printf("[HTTPS] Unable to connect\n");
     }

    postToCloud = false;

  }
  
}


//-------------------------------------------------------------
// Meus handlers
//-------------------------------------------------------------



void handleIrrigaInfo(){
  handleReadInfo();
}

void handleIrrigaChange(){
  String json;
    
  if( irrigaStatus == LOW ){
    irrigaStatus = HIGH;
  } else {
    irrigaStatus = LOW;
  }

  output( IRRIGA, irrigaStatus );
  handleReadInfo();
}

void handleIluminaChange(){
  String json;
    
  if( iluminaStatus == LOW ){
    iluminaStatus = HIGH;
  } else {
    iluminaStatus = LOW;
  }

  output( ILUMINA, iluminaStatus );
  handleReadInfo();
}

void handleIrrigaPulse(){
  handleReadInfo();
  output( IRRIGA, HIGH );
  irrigaStatus = HIGH;
  delay(config.intervalPulse1*1000);
  output( IRRIGA, LOW );
  irrigaStatus = LOW;
}



void handleReloadConfig(){
    loadConfiguration(configFile, config);
    server.send(200, "text/plain", "ok");
}




/*
 * Signal data order
 * - battery level
 * - temperature
 * - humidity
 * - pressure
 * - altitude
 * - actuator 1 status
 * - actuator 2 status 
 * - next actuator 1 schedule in seconds
 * - next actuator 2 schedule in seconds
 */


void handleReadInfo(){
   updateBME();
   batteryValue = analogRead(batteryPin);

  String response;
  response.reserve(128);
  response = (batteryValue-adoffset)*voltsPerUnit;
  response += ";";
  response += temperature;
  response += ";";
  response += humidity;
  response += ";";
  response += pressure;
  response += ";";
  response += altitude;
  response += ";";
  response += irrigaStatus;
  response += ";";
  response += iluminaStatus;
  response += ";";
  server.send(200, "text/plain", response);
}




void dataLogPostToCloud(){
  postToCloud = true;
}



void handleTeste(){

  String response;
  response.reserve(128);
  
  response = "Current time in millis : ";
  response += timeUpdate(); 
  response += " - ";
  response += getFormattedTime( currentTime );
  Serial.println( response );
  server.send(200, "text/plain", response);
}



unsigned long timeUpdate(){
  String response;
  response.reserve(128);
  timeClient.update();
  currentTime = timeClient.getEpochTime();
  return currentTime;
}


String getFormattedTime( unsigned long rawTime ) {
  unsigned long hours = (rawTime % 86400L) / 3600;
  String hoursStr = hours < 10 ? "0" + String(hours) : String(hours);
  unsigned long minutes = (rawTime % 3600) / 60;
  String minuteStr = minutes < 10 ? "0" + String(minutes) : String(minutes);
  unsigned long seconds = rawTime % 60;
  String secondStr = seconds < 10 ? "0" + String(seconds) : String(seconds);
  return hoursStr + ":" + minuteStr + ":" + secondStr;
}


String dumpConfiguration(){

  String response;
  response.reserve(128);
  response = F("Device UUID : ");
  response += config.deviceUUID;
  response += F("\nPort 1 pulse schedule (in seconds) :");
  response += config.schedulePulse1;
  response += F("\nPort 1 pulse interval (in seconds) :");
  response += config.intervalPulse1;
  response += F("\nPort 2 pulse schedule (in seconds) :");
  response += config.schedulePulse2;
  response += F("\nPort 2 pulse interval (in seconds) :");
  response += config.intervalPulse2;

  Serial.println( response );

  return response;  

}



void checkAlarm(){
  timeUpdate();

  //Serial.println(  getFormattedTime( currentTime ) );
}
